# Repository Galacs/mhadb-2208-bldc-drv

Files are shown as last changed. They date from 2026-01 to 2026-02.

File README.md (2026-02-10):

# MHADB BLDC DRIVER

STM32F1 based 2208 size gimbal bldc foc driver controller board

## IC List

- STM32F103C8T (Main MCU)
- DRV8311 (BLDC driver)
- AS5600 (magnetic encoder)
- SN65HVD (CAN transceiver)

# Related repositories

- [Galacs/mhadb-main-board](https://github.com/Galacs/mhadb-main-board)
- [Galacs/mhadb-line-sensor](https://github.com/Galacs/mhadb-line-sensor)
- [Galacs/mhadb-firmware](https://github.com/Galacs/mhadb-firmware)

## Top preview



## Preview 3d render



## Pictures



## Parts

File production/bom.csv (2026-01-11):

Designator | Footprint | Quantity | Value | LCSC Part #
C1, C11, C12, C19, C20, C21, C24, C3, C6, C8 | 0402 | 10 | 0u1 | C307331
C10, C23, C26, C27, C7, C9 | 1206 | 6 | 22u | C12891
C13, C14, C16, C17, C25 | 0402 | 5 | 1u | C52923
C15, C18 | 0402 | 2 | 10n | C15195
C2, C22, C28 | 0805 | 3 | 10u | C440198
C4, C5 | 0603 | 2 | 20p | C1648
D1 | 0805 | 1 | GREEN | C2297
D10, D3, D4, D5, D6, D7, D9 | Diode_DFN1006 | 7 | H5VU10U | C22395519
D11 | 0805 | 1 | YELLOW | C2296
D2 | 0603 | 1 | WHITE | C2290
FB1 | 0805 | 1 | 600Ω@100M | C81034
FB2 | 0805 | 1 | 600Ω@100M | C1015
R1, R10, R2, R8 | 0402 | 4 | 5k1 | C25905
R11, R4, R5, R7, R9 | 0402 | 5 | 10k | C25744
R3 | 1206 | 1 | 120 | C17909
R6 | 0603 | 1 | 560 | C23204
SW1, SW2, SW3 | SW_SPST_TS-1088-xR020 | 3 | SW_Push | C720477
U1 | SOIC-8_3.9x4.9mm_P1.27mm | 1 | SN65HVD230 | C12084
U2 | LQFP-48_7x7mm_P0.5mm | 1 | STM32F103C8Tx | C8734
U3 | Texas_RRW0024A_WQFN-24-1EP_2x2mm_P0.4mmThermalVias | 1 | DRV8311H | C5218862
U4 | SOIC-8_3.9x4.9mm_P1.27mm | 1 | AS5600-ASOT | C499458
Y1 | Crystal_SMD_5032-2Pin_5.0x3.2mm | 1 | 8M | C115962

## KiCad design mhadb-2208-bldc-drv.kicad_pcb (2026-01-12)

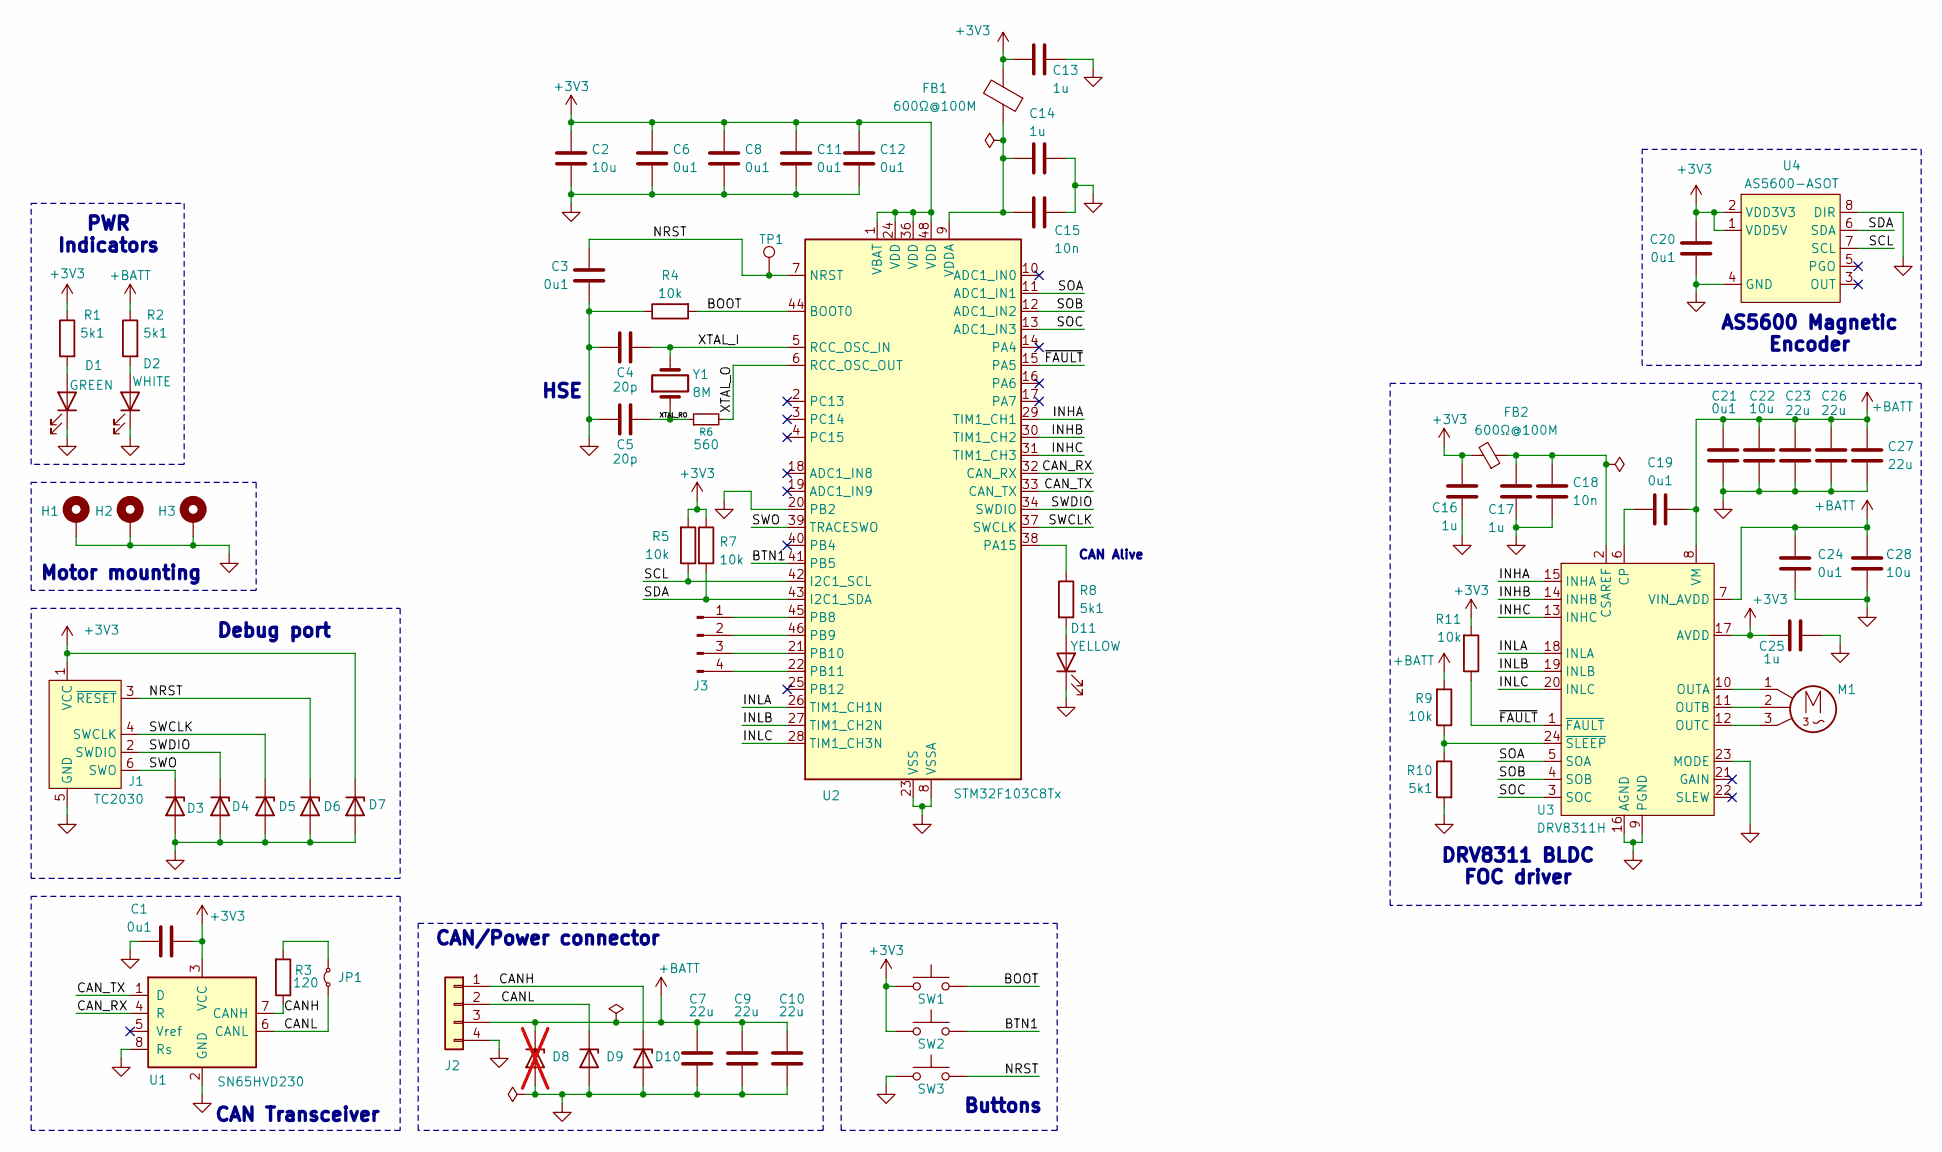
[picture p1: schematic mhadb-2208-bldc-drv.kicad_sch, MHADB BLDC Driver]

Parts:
C1, C3, C6, C8, C11, C12, C19, C20, C21, C24: 0u1; C_0402_1005Metric; Manufacturer Part Number CL05B104KB54PNC; JLCPCB Part # C307331
C2, C22, C28: 10u; C_0805_2012Metric; Manufacturer Part Number GRM21BR61H106KE43L; JLCPCB Part # C440198
C4, C5: 20p; C_0603_1608Metric; Manufacturer Part Number CL10C200JB8NNNC; JLCPCB Part # C1648
C7, C9, C10, C23, C26, C27: 22u; C_1206_3216Metric; Manufacturer Part Number CL31A226KAHNNNE; JLCPCB Part # C12891
C13, C14, C16, C17, C25: 1u; C_0402_1005Metric; Manufacturer Part Number CL05A105KA5NQNC; JLCPCB Part # C52923
C15, C18: 10n; C_0402_1005Metric; Manufacturer Part Number CL05B103KB5NNNC; JLCPCB Part # C15195
D1: GREEN; LED_0805_2012Metric; Manufacturer Part Number KT-0805G; JLCPCB Part # C2297
D2: WHITE; LED_0603_1608Metric; Manufacturer Part Number KT-0603W; JLCPCB Part # C2290
D3, D4, D5, D6, D7, D9, D10: H5VU10U; Diode_DFN1006; Manufacturer Part Number H5VU10U; JLCPCB Part # C22395519
D8: H5VU10U; Diode_DFN1006; Manufacturer Part Number H5VU10U; JLCPCB Part # C22395519; not fitted
D11: YELLOW; LED_0805_2012Metric; Manufacturer Part Number KT-0805Y; JLCPCB Part # C2296
FB1: 600Ω@100M; L_0805_2012Metric; Manufacturer Part Number MPZ2012S601ATD25; JLCPCB Part # C81034
FB2: 600Ω@100M; L_0805_2012Metric; Manufacturer Part Number GZ2012D101TF; JLCPCB Part # C1015
H1, H2, H3: MountingHole_Pad; MountingHole_3.2mm_M3_DIN965_Pad_Thin
J1: TC2030; Tag-Connect_TC2030-IDC-NL_2x03_P1.27mm_Vertical
J2: Conn_01x04; JST_XH_B4B-XH-A_1x04_P2.50mm_Vertical; Manufacturer Part Number B4B-XH-A(LF)(SN); JLCPCB Part # C144395
J3: Conn_01x04_Pin; PinHeader_1x04_P2.54mm_Vertical
JP1: Jumper_2_Small_Bridged; SolderJumper-2_P1.3mm_Open_RoundedPad1.0x1.5mm
M1: Motor_3_Phases; Connector_Pad_1x03
R1, R2, R8, R10: 5k1; R_0402_1005Metric; Manufacturer Part Number 0402WGF5101TCE; JLCPCB Part # C25905
R3: 120; R_1206_3216Metric; Manufacturer Part Number 1206W4F1200T5E; JLCPCB Part # C17909
R4, R5, R7, R9, R11: 10k; R_0402_1005Metric; Manufacturer Part Number 0402WGF1002TCE; JLCPCB Part # C25744
R6: 560; R_0603_1608Metric; Manufacturer Part Number 0603WAF5600T5E; JLCPCB Part # C23204
SW1, SW2, SW3: SW_Push; SW_SPST_TS-1088-xR020; Manufacturer Part Number TS-1088-AR02016; JLCPCB Part # C720477
TP1: TestPoint; TestPoint_Pad_D2.0mm
U1: SN65HVD230; SOIC-8_3.9x4.9mm_P1.27mm; Manufacturer Part Number SN65HVD230DR; JLCPCB Part # C12084
U2: STM32F103C8Tx; LQFP-48_7x7mm_P0.5mm; Manufacturer Part Number STM32F103C8T6; JLCPCB Part # C8734
U3: DRV8311H; Texas_RRW0024A_WQFN-24-1EP_2x2mm_P0.4mmThermalVias; Manufacturer Part Number DRV8311HRRWR; JLCPCB Part # C5218862
U4: AS5600-ASOT; SOIC-8_3.9x4.9mm_P1.27mm; Manufacturer Part Number AS5600-ASOT; JLCPCB Part # C499458
Y1: 8M; Crystal_SMD_5032-2Pin_5.0x3.2mm; Manufacturer Part Number X50328MSB2GI; JLCPCB Part # C115962

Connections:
+3V3: C1.1, C2.1, C6.1, C8.1, C11.1, C12.1, C13.1, C16.1, C20.1, C25.1, D7.1 (K), FB1.2, FB2.2, J1.1 (VCC), R1.1, R5.2, R7.1, R11.2, SW1.1, SW2.1, U1.3 (VCC), U2.1 (VBAT), U2.24 (VDD), U2.36 (VDD), U2.48 (VDD), U3.17 (AVDD), U4.1 (VDD5V), U4.2 (VDD3V3)
+BATT: C7.1, C9.1, C10.1, C19.2, C21.2, C22.2, C23.1, C24.2, C26.1, C27.1, C28.2, D8.1 (K), J2.3, R2.1, R9.2, U3.7 (VIN_AVDD), U3.8 (VM)
/BOOT: R4.2, SW1.2, U2.44 (BOOT0)
/BTN1: SW2.2, U2.41 (PB5)
/CANH: D10.1 (K), J2.1, R3.1, U1.7 (CANH)
/CANL: D9.1 (K), J2.2, JP1.1 (A), U1.6 (CANL)
/CAN_RX: U1.4 (R), U2.32 (CAN_RX)
/CAN_TX: U1.1 (D), U2.33 (CAN_TX)
/INHA: U2.29 (TIM1_CH1), U3.15 (INHA)
/INHB: U2.30 (TIM1_CH2), U3.14 (INHB)
/INHC: U2.31 (TIM1_CH3), U3.13 (INHC)
/INLA: U2.26 (TIM1_CH1N), U3.18 (INLA)
/INLB: U2.27 (TIM1_CH2N), U3.19 (INLB)
/INLC: U2.28 (TIM1_CH3N), U3.20 (INLC)
/NRST: C3.1, D6.1 (K), J1.3 (~RESET), SW3.2, TP1.1, U2.7 (NRST)
/SCL: R5.1, U2.42 (I2C1_SCL), U4.7 (SCL)
/SDA: R7.2, U2.43 (I2C1_SDA), U4.6 (SDA)
/SOA: U2.11 (ADC1_IN1), U3.5 (SOA)
/SOB: U2.12 (ADC1_IN2), U3.4 (SOB)
/SOC: U2.13 (ADC1_IN3), U3.3 (SOC)
/SWCLK: D5.1 (K), J1.4 (SWCLK), U2.37 (SWCLK)
/SWDIO: D4.1 (K), J1.2 (SWDIO), U2.34 (SWDIO)
/SWO: D3.1 (K), J1.6 (SWO), U2.39 (TRACESWO)
/XTAL_I: C4.1, U2.5 (RCC_OSC_IN), Y1.2
/XTAL_O: R6.2, U2.6 (RCC_OSC_OUT)
/XTAL_RO: C5.1, R6.1, Y1.1
/~FAULT: R11.1, U2.15 (PA5), U3.1 (~FAULT)
GND: C1.2, C2.2, C3.2, C4.2, C5.2, C6.2, C7.2, C8.2, C9.2, C10.2, C11.2, C12.2, C13.2, C14.2, C15.2, C16.2, C17.2, C18.2, C20.2, C21.1, C22.1, C23.2, C24.1, C25.2, C26.2, C27.2, C28.1, D1.1 (K), D2.1 (K), D3.2 (A), D4.2 (A), D5.2 (A), D6.2 (A), D7.2 (A), D8.2 (A), D9.2 (A), D10.2 (A), D11.1 (K), H1.1, H2.1, H3.1, J1.5 (GND), J2.4, R4.1, R10.2, SW3.1, U1.2 (GND), U1.8 (Rs), U2.8 (VSSA), U2.20 (PB2), U2.23 (VSS), U2.35 (VSS), U2.47 (VSS), U3.9 (PGND), U3.16 (AGND), U3.23 (MODE), U3.25 (EPAD), U4.4 (GND), U4.8 (DIR)
unnamed: D1.2 (A), R1.2
unnamed: D2.2 (A), R2.2
unnamed: D11.2 (A), R8.2
unnamed: J3.1, U2.45 (PB8)
unnamed: J3.2, U2.46 (PB9)
unnamed: J3.3, U2.21 (PB10)
unnamed: J3.4, U2.22 (PB11)
unnamed: JP1.2 (B), R3.2
unnamed: R8.1, U2.38 (PA15)
unnamed: C14.1, C15.1, FB1.1, U2.9 (VDDA)
unnamed: C19.1, U3.6 (CP)
unnamed: C17.1, C18.1, FB2.1, U3.2 (CSAREF)
unnamed: M1.1, U3.10 (OUTA)
unnamed: M1.2, U3.11 (OUTB)
unnamed: M1.3, U3.12 (OUTC)
unnamed: R9.1, R10.1, U3.24 (~SLEEP)

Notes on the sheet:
Motor mounting
PWR Indicators
Debug port
HSE
CAN/Power connector
CAN Alive
AS5600 Magnetic Encoder
DRV8311 BLDC FOC driver
CAN Transceiver
Buttons

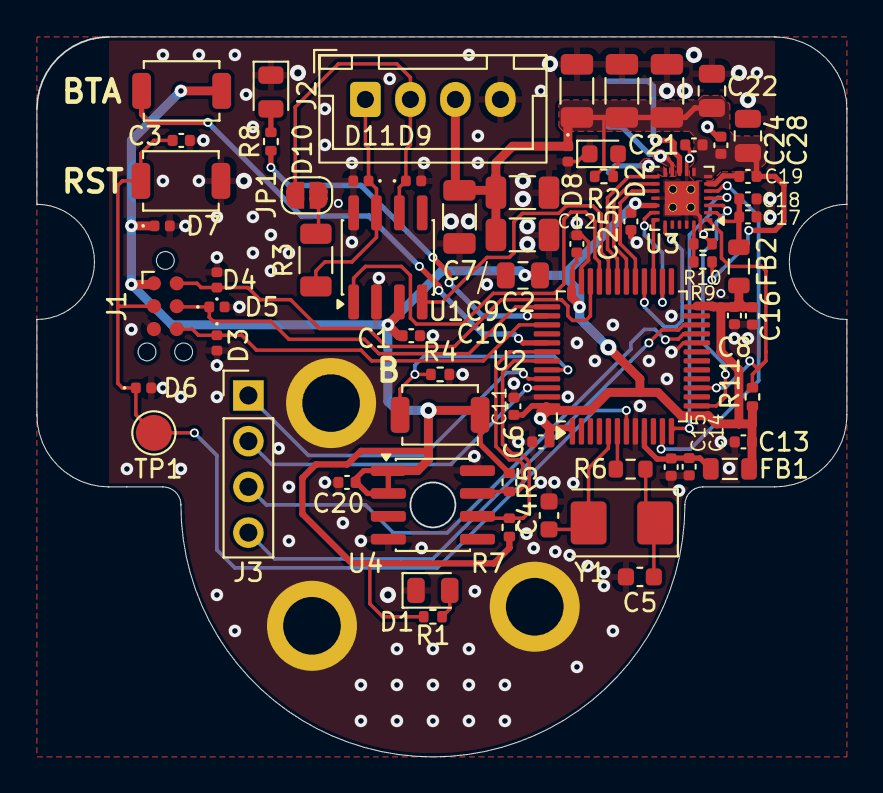
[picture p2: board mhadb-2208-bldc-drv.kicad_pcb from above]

Board: 2 copper layers, 45.0 x 40.0 mm, 69 parts (1 on the bottom side), 44 nets.

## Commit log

2026-01-09 schem: import STM32F103C8Tx from line sensor
    [mhadb-2208-bldc-drv.kicad_sch]
2026-01-09 schem: add buttons
    [mhadb-2208-bldc-drv.kicad_sch]
2026-01-09 schem: add CAN/Power connector
    [mhadb-2208-bldc-drv.kicad_sch]
2026-01-09 schem: add CAN transceiver
    [mhadb-2208-bldc-drv.kicad_sch]
2026-01-09 schem: add SWD tag connect
    [mhadb-2208-bldc-drv.kicad_sch]
2026-01-09 schem: add HT753-1 3V3 LDO
    [mhadb-2208-bldc-drv.kicad_sch]
2026-01-09 schem: add DRV8311 BLDC FOC driver
    [mhadb-2208-bldc-drv.kicad_sch]
2026-01-09 schem: add AS5600 magnetic encoder
    [mhadb-2208-bldc-drv.kicad_sch]
2026-01-09 schem: add net classes
    [mhadb-2208-bldc-drv.kicad_sch]
2026-01-09 pcb: create file and import
    [mhadb-2208-bldc-drv.kicad_pcb]
2026-01-09 pcb: import components from schema
    [mhadb-2208-bldc-drv.kicad_pcb]
2026-01-09 schem/pcb: add motor mounting holes
    [mhadb-2208-bldc-drv.kicad_pcb, mhadb-2208-bldc-drv.kicad_sch]
2026-01-09 pcb: add edge cut
    [mhadb-2208-bldc-drv.kicad_pcb]
2026-01-10 schem/pcb: fix DRV8311 nsleep
    [mhadb-2208-bldc-drv.kicad_pcb, mhadb-2208-bldc-drv.kicad_sch]
2026-01-10 pcb: add edge mounting keepout area
    [mhadb-2208-bldc-drv.kicad_pcb]
2026-01-10 pcb: initial rough placement
    [mhadb-2208-bldc-drv.kicad_pcb, mhadb-2208-bldc-drv.kicad_sch]
2026-01-10 pcb: initial components placement
    [mhadb-2208-bldc-drv.kicad_pcb, mhadb-2208-bldc-drv.kicad_sch]
2026-01-10 pcb: reduce pcb width to 45m
    [mhadb-2208-bldc-drv.kicad_pcb]
2026-01-10 schem: set DNP on wrongly rated tvs diode
    [mhadb-2208-bldc-drv.kicad_pcb, mhadb-2208-bldc-drv.kicad_sch]
2026-01-10 schem: add power led indicators
    [mhadb-2208-bldc-drv.kicad_sch]
2026-01-10 schem: add BTN
    [mhadb-2208-bldc-drv.kicad_sch]
2026-01-10 schem: add missing info to BOM
    [mhadb-2208-bldc-drv.kicad_sch]
2026-01-10 schem: renumber
    [mhadb-2208-bldc-drv.kicad_sch]
2026-01-10 schem: add title
    [mhadb-2208-bldc-drv.kicad_sch]
2026-01-10 pcb: update from schema
    [mhadb-2208-bldc-drv.kicad_pcb, mhadb-2208-bldc-drv.kicad_sch]
2026-01-10 pcb: add gnd planes
    [mhadb-2208-bldc-drv.kicad_pcb]
2026-01-10 pcb: add gnd vias
    [mhadb-2208-bldc-drv.kicad_pcb]
2026-01-10 pcb: route crystal
    [mhadb-2208-bldc-drv.kicad_pcb, mhadb-2208-bldc-drv.kicad_sch]
2026-01-10 pcb: route SWD
    [mhadb-2208-bldc-drv.kicad_pcb]
2026-01-10 pcb: route CAN
    [mhadb-2208-bldc-drv.kicad_pcb]
2026-01-10 pcb: route DRV8311
    [mhadb-2208-bldc-drv.kicad_pcb]
2026-01-10 pcb: route AS5600
    [mhadb-2208-bldc-drv.kicad_pcb]
2026-01-10 pcb: route +BATT power
    [mhadb-2208-bldc-drv.kicad_pcb]
2026-01-10 pcb: route spare GPIOs
    [mhadb-2208-bldc-drv.kicad_pcb]
2026-01-10 pcb: route +3v3 PWR
    [mhadb-2208-bldc-drv.kicad_pcb]
2026-01-10 pcb: route BOOT and RST
    [mhadb-2208-bldc-drv.kicad_pcb]
2026-01-10 pcb: route BTN and CAN status
    [mhadb-2208-bldc-drv.kicad_pcb]
2026-01-10 pcb: add stitching vias
    [mhadb-2208-bldc-drv.kicad_pcb]
2026-01-10 pcb: run and fix DRC
    [mhadb-2208-bldc-drv.kicad_pcb]
2026-01-11 pcb(silkscreen): clean reference designators
    [mhadb-2208-bldc-drv.kicad_pcb]
2026-01-11 pcb(silkscreen): add user txt
    [mhadb-2208-bldc-drv.kicad_pcb]
2026-01-11 add production files
    [bom.csv, designators.csv, positions.csv]
2026-01-11 pcb(silkscreen): add front buttons text
    [mhadb-2208-bldc-drv.kicad_pcb]
2026-01-11 pcb: add title
    [mhadb-2208-bldc-drv.kicad_pcb]
2026-01-11 update BOM
    [mhadb-2208-bldc-drv.kicad_pcb, mhadb-2208-bldc-drv.kicad_sch]
2026-01-11 regenerate production files
    [bom.csv]
2026-01-12 pcb: update wheel 3d modell
    [mhadb-2208-bldc-drv.kicad_pcb]
